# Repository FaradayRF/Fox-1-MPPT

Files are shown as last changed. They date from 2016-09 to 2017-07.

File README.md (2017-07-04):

# Fox-1-MPPT
This repository contains the Public Domain files of the [Radio Amateur Satellite Corporation](http://www.amsat.org) (AMSAT) Fox-1 satellite Maximum Power Point Tracker. This is a PCBA flying on the Fox-1 series of 1U cubesats which optimizes the power extracted from the six solar panels on the spacecraft using analog computing.

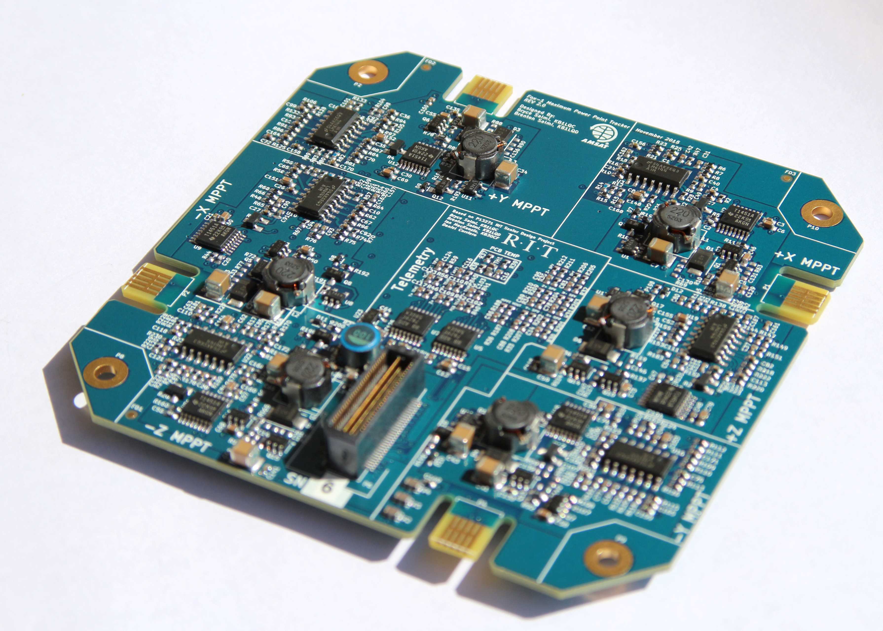
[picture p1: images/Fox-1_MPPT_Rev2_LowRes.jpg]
AMSAT Fox-1 MPPT


# Overview

The Fox-1 Maximum Power Point Tracker utilizes analog computing to track the solar panel voltage which generates the maximum amount of power from solar cells. It implements what is essentially a "temperature-based set-point constant voltage algorithm" MPPT. Since the solar cells are well-known, this design uses op-amps to compute the predicted voltage which will produce maximum power as fast as the analog bandwidth of the components used will allow it. Analog MPPT was chosen for it's "stateless" design due to radiation tolerance concerns of microcontrollers.

Revision 1.2 boards are Revision 1 PCB's with BOM modifications necessary for correct operation. This included stacking some capacitors ontop of feedback resistors in the RTD circuit for stability. Revision 1 PCB's are green soldermask in color. Revision 2 PCB's were created to adress these issues better and properly mount all parts with correct footprints and adress some other manufacturing needs. These boards are use a blue soldermask and the design files for the Rev 2.1 boards have been uploaded to this Github repository.

[READ THE FOX-1 MPPT TECHNICAL OVERVIEW TO UNDERSTAND THE PROJECT!](https://github.com/FaradayRF/Fox-1-MPPT/blob/master/Documents/Fox-1_MaximumPowerPointTracker.pdf)

# History
This project began as a [Rochester Institue of Technology](http://downloads.kicad-pcb.org/archive/KiCad_stable-2013.07.07-BZR4022_Win_full_version.exe) Multi-disciplinary Senior Design (MSD) project during the 2012-2013 school year. Originally the [P13271 AMSAT-MPPT](http://edge.rit.edu/edge/P13271/public/Home) project which successfully delivered a proof-of-concept MPPT intended for a 3U cubesat, the design was continued and modified for use on the smaller Fox-1 satellites which are 1U in size.

## Original Team
The original RIT team to create this MPPT included
* Bryce Salmi, KB1LQC
* Brenton Salmi, KB1LQD
* Ian MacKenzi, KB3OCF
* Daniel Corriero

Work was performed over two years between 2013 and 2015 by Bryce Salmi and Brenton Salmi to bring the design to flight status from the P13271 project as seen here.

# Flights
The Revision 1.2 and Revision 2.1 Maximum Power Point Trackers are currently slated to fly on several launches to Low Earth Orbit with more launches being sought after. These flights are accurate as of 9/3/2016.

### Fox-1Cliff and Fox-1D
Two MPPTs will fly aboard two cubesats on the same launch. These satellites are Fox-1Cliff and Fox-1D which are being sent up on the Spaceflight SHERPA payload on a [SpaceX Falcon 9](http://www.spacex.com/falcon9).

### Fox-1B "RadFxSat"
One MPPT will be flying on the Fox-1B cubesat set to launch aboard a ULA [Delta II](http://www.ulalaunch.com/Products_DeltaII.aspx) rocket.

### Fox-1E "RadFxSat-2"
One MPPT will be flying on the Fox-1E cubesat set to launch aboard a [Virgin Galactic Launcher One](http://www.virgingalactic.com/satellite-launch/) in December, 2017.

# Project Structure
## Hardware Files
All hardware files are located in the [Hardware/Rev2_1](https://github.com/FaradayRF/Fox-1-MPPT/tree/master/Hardware/Rev2_1) directory. They consist of [Kicad EDA](http://kicad-pcb.org/) files which were developed using [Kicad Build: 2013-07-07 BZR 4022](http://downloads.kicad-pcb.org/archive/KiCad_stable-2013.07.07-BZR4022_Win_full_version.exe) which is the July 2013 stable version of the EDA tool (Windows). Also placed into the hardware directory are the [project output files](https://github.com/FaradayRF/Fox-1-MPPT/tree/master/Hardware/Rev2_1/OutputFiles). These are the files which were used to order the PCBs and present an easy to use view of the design (PDF, Excel, Gerber, etc).

**Notable Documents**
* [MPPT Schematic PDF Export](https://github.com/FaradayRF/Fox-1-MPPT/blob/master/Hardware/Rev2_1/OutputFiles/TL1451_MPPT_Flight_Rev2_BW.pdf)
* [MPPT BOM](https://github.com/FaradayRF/Fox-1-MPPT/blob/master/Hardware/Rev2_1/OutputFiles/TL1451_MPPT_Flight_Rev2_BOM.xlsx)
* [MPPT Extra Components BOM](https://github.com/FaradayRF/Fox-1-MPPT/blob/master/Hardware/Rev2_1/OutputFiles/TL1451_MPPT_Flight_Rev2_Additional_BOM.xlsx)
 * Addition parts for the solar panels necessary for the MPPT to work
* [MPPT KiCad project file](https://github.com/FaradayRF/Fox-1-MPPT/blob/master/Hardware/Rev2_1/TL1451_MPPT_Flight_Rev1.pro)
* [KB1LQC KiCad schematic symbol library](https://github.com/FaradayRF/Fox-1-MPPT/blob/master/Hardware/Rev2_1/KB1LQC.lib)
* [KB1LQC KiCad PCBNew footprint library](https://github.com/FaradayRF/Fox-1-MPPT/blob/master/Hardware/Rev2_1/KB1LQC.mod)
* [MPPT PCB Fabrication Files](https://github.com/FaradayRF/Fox-1-MPPT/blob/master/Hardware/Rev2_1/OutputFiles/TL1451_MPPT_Flight_Rev2_1_FAB_Files.zip)
* [MPPT PCBA Assembly Files](https://github.com/FaradayRF/Fox-1-MPPT/blob/master/Hardware/Rev2_1/OutputFiles/TL1451_MPPT_Flight_Rev2_1_ASSEMBLY_Files.zip)

## Documents
The [documents folder](https://github.com/FaradayRF/Fox-1-MPPT/tree/master/Documents) contains support documents necessary to describe the design intentions and analysis of the MPPT.

**Notable Documents**
* [Fox-1 MPPT Technical Overview](https://github.com/FaradayRF/Fox-1-MPPT/blob/master/Documents/Fox-1_MaximumPowerPointTracker.pdf)
* [Fox-1 Satellite Solar Panel Calculations](https://github.com/FaradayRF/Fox-1-MPPT/blob/master/Documents/MPPT_Expected_Voltages_Fox-1.xlsx)
* [Fox-1 Solar Panel Telemetry Scaling](https://github.com/FaradayRF/Fox-1-MPPT/blob/master/Documents/PanelTemperatureScaling.xlsx)
 * Scaling telemetry downlinked from satellite over RF into Celcius from RTD circuit

## Images
The [images directory](https://github.com/FaradayRF/Fox-1-MPPT/tree/master/images) contains a select set of high-quality stock images showing the Rev 2 MPPT very clearly. Not much more needed to say about this :rocket:

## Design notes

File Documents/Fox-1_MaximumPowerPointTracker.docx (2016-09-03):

Date: September 3rd, 2016

Version: 1.2

Author: Bryce Salmi, KB1LQC

AMSAT Fox-1 Maximum Power Point Tracker

## Introduction

The Radio Amateur Satellite Corporation, AMSAT, has designed and built a series of 1U Cubesats referred to as Fox-1. Starting with these 1U Cubesats, AMSAT will build up intellectual property to leverage onto future satellite designs. A requirement for the Fox-1 satellites is an efficient way to maximize power generation from solar cells with a scalable Maximum Power Point Tracker, MPPT. Based on the Fox-2 design originally conceived by the P13271 senior design team (http://edge.rit.edu/edge/P13271/public/Home)[^1] at the Rochester Institute of Technology AMSAT has developed a radiation tolerant analog MPPT for use on the Fox-1 satellites. Lessons learned building the Fox-1 MPPT detailed in this document can also be rolled into any future Fox-2 MPPT design.

### Document History

DATE | VERSION | SUMMARY
January 21, 2015 | 1.0 | Initial creation of document
October 2, 2015 | 1.1 | Initial flight design
September 3, 2016 | 1.2 | MPPT Rev 1.2 and 2 Updates

### Document Scope

The purpose of this document is to clearly explain how the Fox-1 MPPT has been designed, how it operates, and to how any known failure modes or risks affect the spacecraft. PCB revision 1.1 is shown in this document but the design of Rev 1.2 and Rev 2 are discussed. It also assumes a basic level of electrical knowledge and leaves some calculations up to the reader with reference material noted.

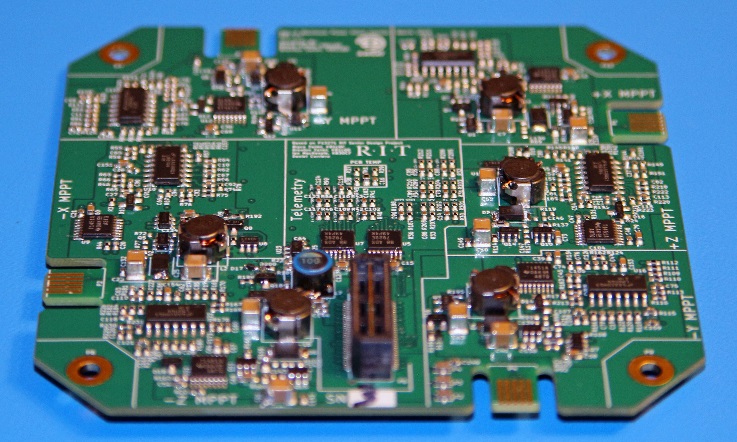
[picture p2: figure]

Figure 1: Fox-1 MPPT Rev 1.1

# Overview

The Fox-1 MPPT PCB contains six set-point constant voltage MPPT circuits[^2] with a single MPPT dedicated to each side of the spacecraft. Every side of Fox-1 contains two Spectrolab UTJ solar cells connected in series. All six MPPTs are combined through ideal diodes which allows for power sharing as the satellite rotates in orbit. The common diode OR’d output node then delivers the combined power of all sufficiently illuminated solar panels to the spacecraft main voltage bus. The Fox-1 MPPT also contains a telemetry circuit able to communicate with the Internal Housekeeping Unit, IHU, via I²C communications. It’s important to note that each of the six MPPTs is a zero fault tolerant design.

## Specifications

Parameter | Value | Units
Maximum Input Voltage | 50 | Volts
Minimum Input Voltage | 3.6 | Volts
Maximum Input Current (Per MPPT) | 0.443 | Amperes
Maximum Input Power (Per MPPT) | 2.57 | Watts
Maximum Output Current (Per MPPT) | 0.780 | Amps @ 3.3V Vout
Maximum Output Voltage | 4.33V | Volts
Maximum Switching Efficiency | ~88 | %
Maximum Tracking Error | +-5 | %
Temperature Range of Components | -40° to +125° | Celsius
Solar Cell Operating Temperature Range | -60° to +60° | Celsius

Table 1: Overall Fox-1 MPPT Specifications

Careful use of radiation tested components, shielding, and a stateless design in the critical MPPT feedback loops on Fox-1 has been implemented in order to promote a 5 year mission timeline and an estimated 30 kRad TID exposure. The stateless design hardens the MPPT to Single Event Upsets, SEU, and Single Event Latch-ups, SEL, which are expected during the mission. Table 1 documents the general specifications achieved as supported by engineering bring-up data.

## Spectrolab UTJ Solar Cells

Fox-1 was designed for use with two SpectroLab UTJ solar cells (http://www.spectrolab.com/DataSheets/TNJCell/utj3.pdf) in series on each solar panel with each cell having 27 cm² of area as shown in Figure 2. Table 11 in the Appendix shows the calculations of the maximum power point thermal drift. This information was used to design the MPPT as well as predict the amount of power available to Fox-1 at any panel temperature expected in orbit. The RTD measuring panel temperature is mounted to the back side of the solar panels out of direct sunlight.

Figure 2: Solar panels on Fox-1, a stowed antenna is shown on the closest facing solar panel

## MPPT PCB Configuration

### PCB Block Diagram

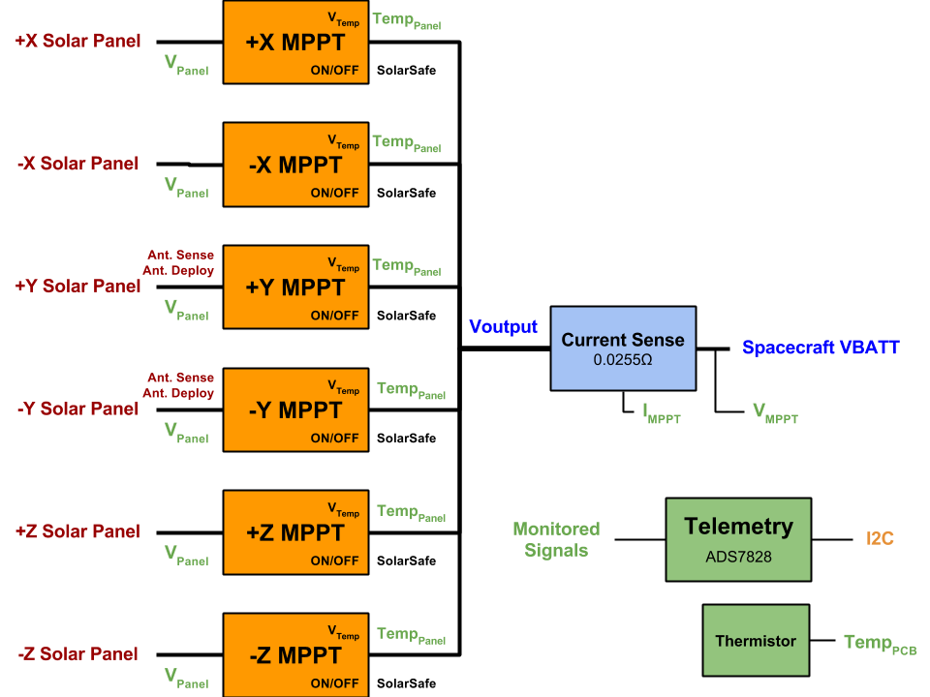
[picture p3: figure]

Figure 3: Fox-1 MPPT PCB block diagram containing six individual MPPT circuits combined together

Six Individual Maximum Power Point Trackers obtain power from their respective solar panels and if sufficient power is available then combine the generated power onto a common output
node through ideal diodes. The combined power is then fed through a current sense circuit before being sent to the Fox-1 “VBATT” node to power the satellite and charge the batteries. A telemetry system comprised of voltage dividers, RC low pass filters, and ADC’s gather engineering data for transmission to the IHU via I²C communications.

The design of the Fox-1 MPPT does not require a battery on the output of the PCB for proper operation. In the event of a battery failure where a properly designed circuit will disconnect the battery from the satellite power bus, the MPPT is fully capable of operation. The requirement for this operation however is that no more than maximum power available from the MPPT can be requested from the payload. This means that if the satellite can operate by never drawing more power than the lowest power available from solar panels then indefinite operation without a battery is possible.

Power is obtained from the X and Y axis panels through PCB edge connectors (Samtec MEC1-105-02-L-D-NP-A) and through the board-to-board connectors (Samtec QSH-030-01-L-D-A and QTH-030-02-L-D-A). Besides solar power, signals passing through these PCB edge connectors are the RTD connections (ground referenced) for measurement of each solar panel temperature as well as two antenna deploy and sense channels on the Y panels. The antenna deploy and sense connections are not thoroughly covered in this document, please refer to the schematic. All copper planes have been pulled back from the connector and a maximum of 20 mil traces were used to the connectors themselves to prevent heat loss to space from the MPPT PCB which is necessary for proper operation

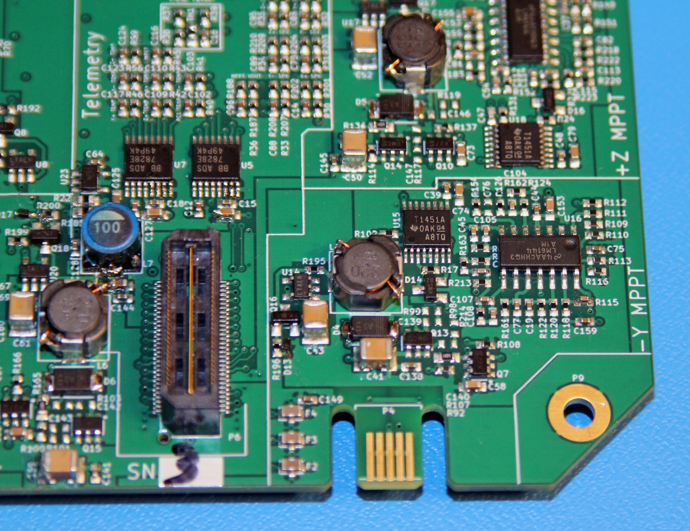
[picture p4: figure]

Figure 4: Samtec QTH-030-02-L-D-A board to board connector shown on left side of image, Samtec MEC1-105-02-L-D-NP-A edge connector shown near middle of image with male portion of connector made of PCB material

## PCB Design

Each PCB is a four layer board developed in the open source KiCad EDA (http://www.kicad-pcb.org/display/KICAD/KiCad+EDA+Software+Suite) (Build: 2013-07-07 BZR 4022)-stable on Windows. Gerber files were exported and sent to Advanced Circuits for fabrication. Since Gerbers are very portable file formats, AMSAT has the ability to use almost any manufacturer they choose. All relevant PCB processes have been documented in the “Drawings” Layer of the Gerbers.

### PCB Stackup

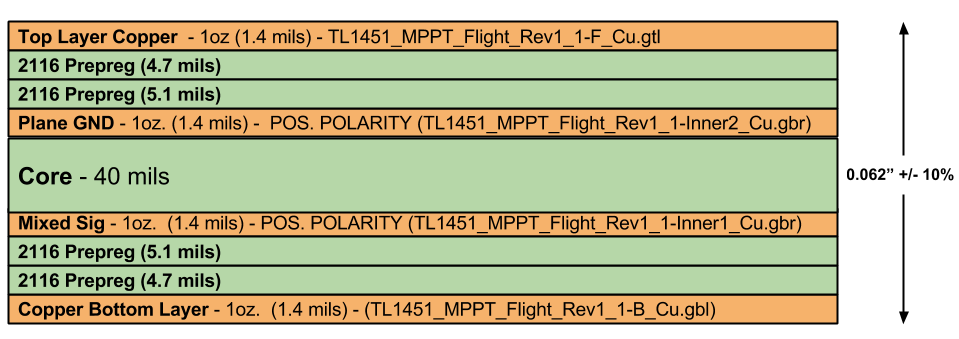
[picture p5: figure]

Figure 5: Four layer PCB stackup used on the Fox-1 MPPT Rev 1.1 PCB

Figure 6: Fox-1 MPPT Rev 1.1 PCB with top layer visible, all components other than stacking connector located on top layer

# Maximum Power Point Tracker Design

## MPPT Overview

The Fox-1 MPPT is designed as a temperature based set-point constant voltage MPPT and is implemented with analog circuitry to mitigate radiation events associated with holding state. There are two discrete feedback loops implemented in the design, the MPPT feedback loop and an output voltage regulation feedback loop. Both MPPT feedback loop and MPPT as a PCB will be referred to in this document and the context will determine the subject. The output voltage regulation circuitry limits the MPPT channel output voltage to 4.33V prior to the ideal diodes in order to protect the Fox-1 payload and batteries from overvoltage conditions. Using temperature based MPPT allowed power to be maximized without computational resources such as a microcontroller which requires state.

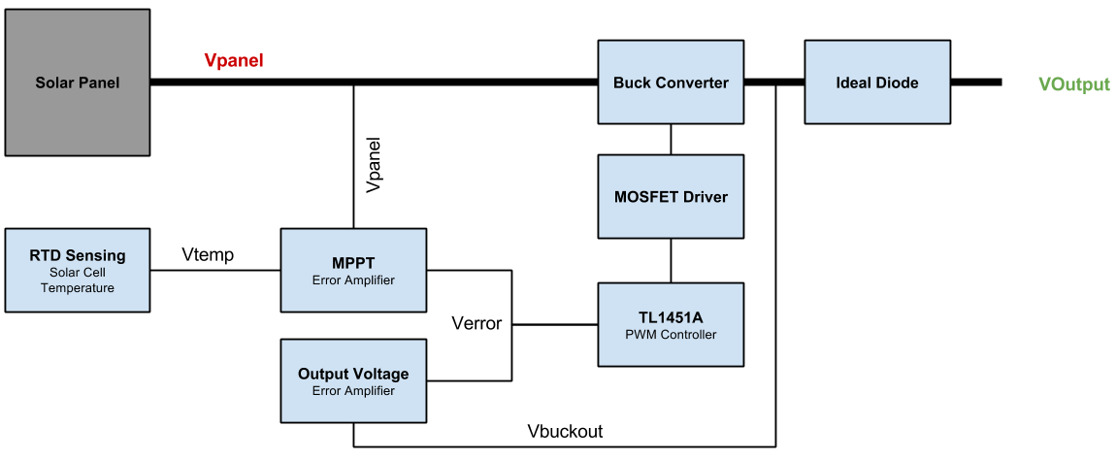
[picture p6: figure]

Figure 7: Fox-1 MPPT & voltage regulation feedback block diagram

As shown in Figure 7, there are two feedback loops used to control the TL1451A PWM controller. The internal TL1451A error amplifier is used as a unity gain buffer to directly pass the combined V_(error) signal from the external error amplifiers into the internal comparator used to generate the PWM signal. The inversions from the TL1451A open collector PWM output and PMOS gate create the following V_(error) to duty cycle relationship shown in Table 2.

V_(error) Change | PWM Duty Cycle
Increasing | Decreasing
Decreasing | Increasing

Table 2: Error voltage effect on the PWM duty cycle

Therefore, a simple resistive adder is used to combine both the MPPT error amplifier and output voltage regulation error amplifier signals. This results in the highest voltage error signal applied to the TL1451A winning control of the buck converter and forcing the lowest duty cycle of the two feedback loops to be implemented. This is extremely advantageous as shown later in this document.

## MPPT Schematics

The latest version of the schematics for the Fox-1 MPPT are located in the AMSAT SVN MPPT folder (http://amsatfox.org/repos/Fox1/PSU/MPPT/tags/Rev1_1/). Using KiCad to open “TL1451_MPPT_Flight_Rev1.pro” one has access to the schematics and PCB files within the KiCad EDA. An important note is that the libraries and footprints used for KiCad live in the SVN Power KiCad folder (http://amsatfox.org/repos/Power/kicad/) so those must be checked out too and Kicad may need to be told where they are on your computer to display properly. An annotated PDF version of the schematics is provided with this document.

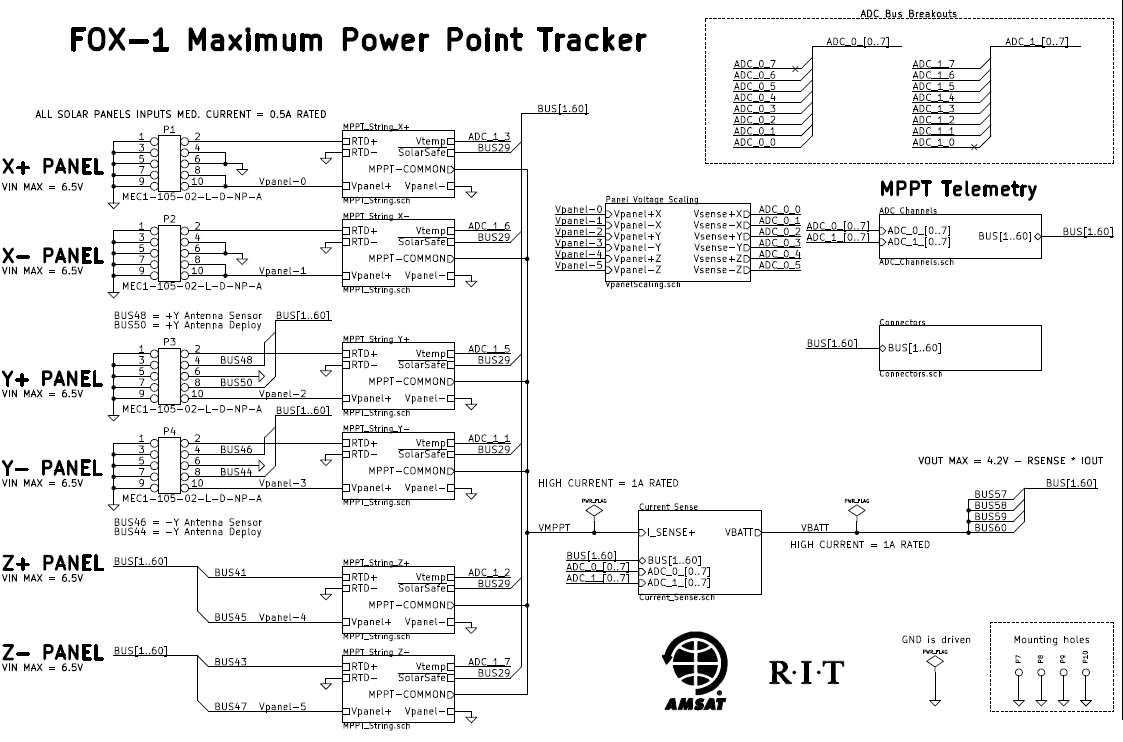
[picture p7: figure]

Figure 8: Main schematic page of the Fox-1 MPPT closely resembling the block diagram in Figure 3

The schematics are built up in a hierarchical arrangement as shown in Figure 8 much like block diagrams that contain sub-circuits within individual blocks. This makes understanding signal flows much easier and is very different from how EAGLE presents schematics. The main schematic page looks a lot like the overview block diagram shown in Figure 3. Hierarchical design results in a large number of schematics sheets due to channelization of the design. An annotated schematic included with this document at the 2015 AMSAT Symposium details all unique MPPT PCB circuits without duplication.

### Resistive Temperature Detector Circuitry

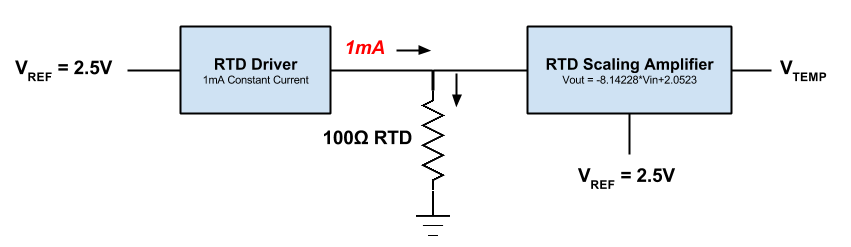
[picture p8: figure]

Figure 9: RTD drive and sensing block diagram

The AMSAT MPPT uses resistive temperature detectors, RTDs, to accurately measure solar panel temperature which is then used to predict the Maximum Power Point Voltage, MPPV. A constant current source forces exactly 1 mA into the RTD leaving only voltage to change with varying resistance as the RTD changes temperature. Both voltage and resistance are directly correlated as governed by Ohms law when using a constant current source. The measured voltage developed across the RTD is conditioned and amplified using a simultaneous equation based op-amp circuit implementing analog mathematics. This produces a voltage mimicking the solar panel voltage at MPPV and can be referenced by the MPPT error amplifier as it compares real panel voltage against this predicted reference voltage. This scaled voltage produced by the amplifier is referred to as V_(temp) . The RTD used for each panel is a PT100 type device, nominally 100Ω at 0°C (PTS080501B100RP100 (http://www.vishay.com/docs/28762/ptsserie.pdf)). RTDs are not thermistors, they use a pure metal such as nickel or platinum which have very accurate and predictable changes in resistance over temperature and nearly linear responses over the temperature ranges used.

Figure 10: Fox-1 MPPT RTD constant current driver

U3A of Figure 10 is a LM6144A op-amp configured as a constant 1 mA source. Its sole purpose is to force exactly 1 mA of current through the RTD. Note, C168 is used to slow down the op-amp to prevent oscillations. Figure 11 shows a LTSpice schematic of the 1 mA RTD driver (http://amsatfox.org/repos/Fox1/PSU/MPPT/Simulations/Flight_Current_Source.asc) and is used to describe the RTD circuit for the remainder of this description. The following equation determines the output voltage of the op-amp U1:

Vout=V_2 ((R_4)/(R_3 +R_4))×((R_2 +R_1)/(R_2))-V_1 ×(R_1)/(R_2)

Where V_2 is the reference voltage and V_1 is the grounded pad of R_1 . However, since R_1 ,R_2 ,R_3 , and R_4 are all 249KΩ we simplify the equation down to:

V_(OUT) =V_2 - V_1 =2.5 V

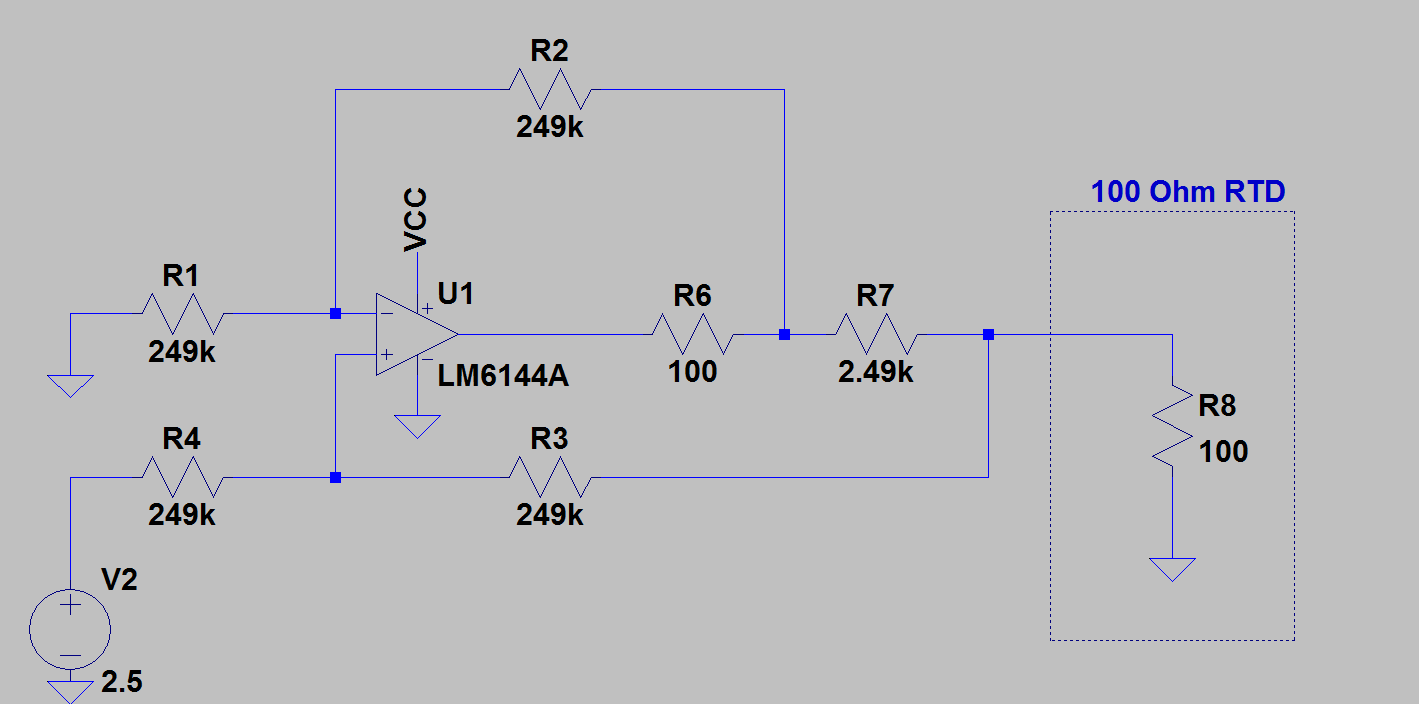
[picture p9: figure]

Figure 11: LTSpice 1mA RTD drive simulation schematic, capacitors not simulated.

Knowing we have 2.5V across R7 due to op-amp laws the following relationship for drive current is made.

R_7 =(V_2)/(I_(Drive))= (2.5V)/(1mA)=2.5KΩ

With 1 mA of drive current being forced into R8 (a 100Ω RTD) the voltage across it is predictable thanks to Ohms Law. 1 mA of drive current will dissipate about 100uW of power in the RTD and therefore cause minimal internal self-heating of the device and allows for accurate measurements. Table 3 shows several data points along the operating conditions expected in orbit for the solar panels and the respective RTD circuit voltage.

RTD Temperature | Voltage Across RTD
-60°C | 0.076V
0°C | 0.100V
28°C | 0.111V
+60°C | 0.124V

Table 3: Expected RTD voltages at 1mA drive current

The voltage across the RTD is very small (between 76mV and 124mV) and exhibits a positive thermal coefficient. This means the voltage increases as the temperature increases. However, the solar cells exhibit a negative temperature coefficient since the MPPT voltage decreases with a temperature increase. An op-amp configured to follow a polynomial equation is used to amplify the measured RTD voltage and flip the RTD voltage thermal coefficient. Essentially the op-amp performs the function y= -mX+b as covered in SLOA076 (http://www.ti.com/lit/ml/sloa076/sloa076.pdf) from Texas Instruments. The flight conditioning circuit implementing analog mathematics is shown in Figure 12. Note that the feedback capacitor C162 is used to slow down the op-amp and prevent oscillations.

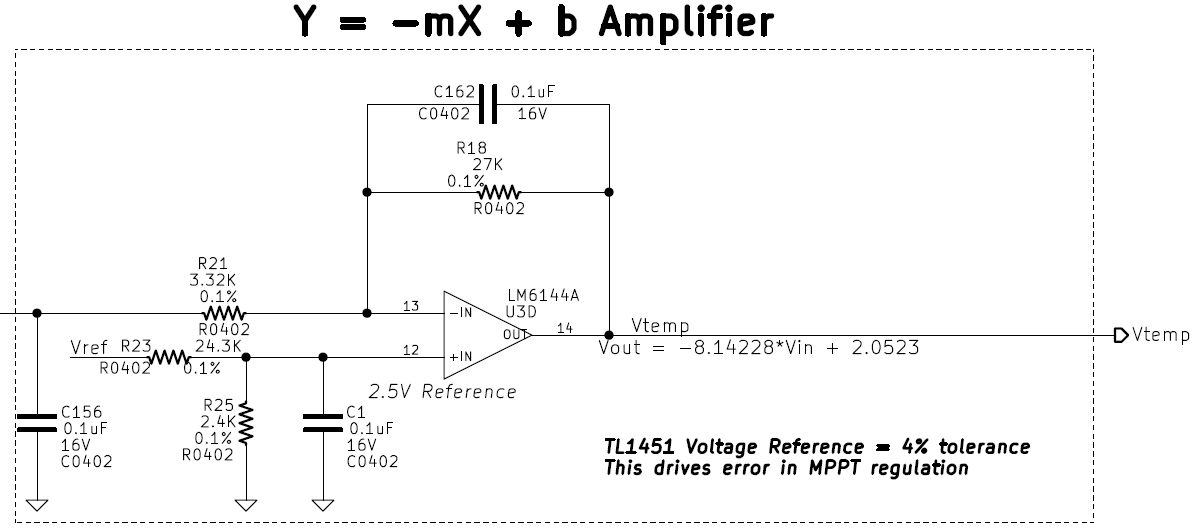
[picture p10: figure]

Figure 12: Scaling amplifier implemented on the Fox-1 MPPT panel temperature circuit which mimics solar panel MPPV

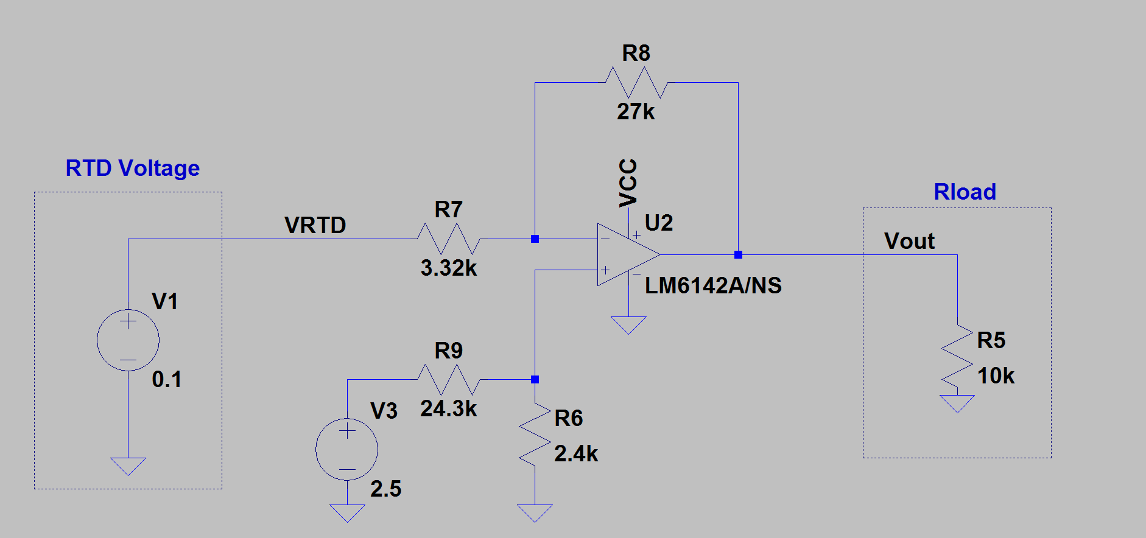
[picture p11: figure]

Figure 13: An LTSpice simulation of the RTD scaling amplifier, capacitors not simulated

Figure 13 shows the LTSpice simulation of the RTD conditioning amplifier referenced in the following description. Voltage source V1 represents the RTD voltage being measured and V3 represents the 2.5V reference from the TL1451A. A capacitor is added in the flight circuit across R6 to ground to low pass filter the voltage reference as shown in Figure 12. Another capacitor has been placed across R8 in the flight circuit to reduce the bandwidth of the circuit for stability also shown in Figure 12. A differential amplifier was not used to buffer the RTD since the solar panel PCBs have already been produced and were designed for thermistors which have one of the pins grounded and therefore the RTDs have a grounded pin too, rendering a differential amplifier not effective.

The TL1451A recommended error amplifier input voltage range is 1.05V to 1.45V so the panel voltage has been scaled by 0.245 using voltage dividers before being measured. The RTD predicted panel voltage must mimic this scaled voltage. The voltages in the Fox-1 Solar Panel Calculations in the Appendix show that minimum MPPV is obtained when high temperature panels are tracked at 4.28V and the maximum MPPV is 5.84V when the panels are tracked at low temperatures. This results in a MPPV voltage range of 1.048V to 1.430V present at the MPPT error amplifier during nominal power point tracking. These voltages are used as part of the simultaneous equations solved in SLOA076 (http://www.ti.com/lit/ml/sloa076/sloa076.pdf) and are given in Table 4 which are used to translate RTD measured voltages into the predicted MPPV reference voltage V_(temp) . The predicted voltage is also telemetered to sense panel temperature remotely from Earth via RF telemetry. With some basic mathematics described in the ADC section of this document the panel temperature can be resolved back from this voltage as measured by the ADC.

RTD Temperature | RTD Voltage | Vout Desired
60°C | 0.124V | 1.048V
-60°C | 0.076V | 1.430V

Table 4: Voltages used to solve for the scaling amplifiers component values

The values used for the output voltage of the scaling amplifier were chosen based on obtainable resistor values resulting in the following equation relating Vout of Figure 13 to RTD voltage:

V_(OUT) = -8.14228∙V_(IN) +2.0523

Figure 14 shows the RTD voltage versus scaling amplifier output voltage (predicted MPPV). The amplifier clearly amplifies the voltage as well as flips the temperature coefficient to match the Spectrolab solar cell based panel temperature coefficient.

Figure 14: Simulated RTD voltage input to the amplifier and output voltage representing the scaled panel voltage desired. The top graph shows the RTD voltage over the expected operating range while the bottom graph shows the resulting op-amp output voltage for the

### Totem Pole MOSFET Driver

The PWM output from the TL1451A is an open collector circuit and cannot provide a low impedance drive signal into the switching MOSFET gate. A low impedance drive signal is necessary to quickly turn the MOSFET on and off. A pull-up resistor, R11 in Figure 15, is connected to the open collector pin of the TL1451A where the PWM signal is output. More information can be found regarding MOSFET drivers in SLUP169 (http://www.ti.com/lit/ml/slup169/slup169.pdf) from TI.

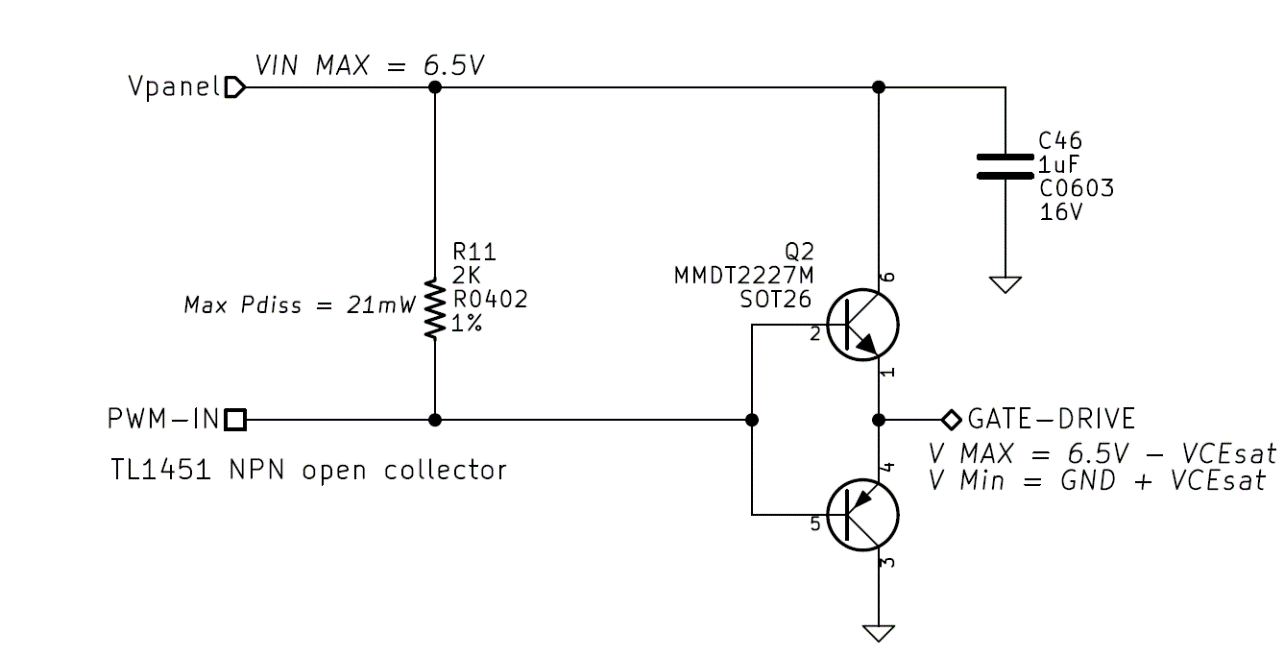
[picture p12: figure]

Figure 15: Open collector PWM output and totem pole MOSFET driver

The TL1451A output open collector stage inverts the signal produced by the PWM generator which is then fed into the totem pole driver (Q2 in Figure 15) which is a non-inverting circuit. The totem pole operates by pulling the MOSFET gate close to ground or close to the solar panel voltage, well into saturation or cutoff of the switching MOSFET. When the TL1451A open collector output pulls towards ground this will cause the PNP transistor base of Q2 (pin 5) to be a lower voltage than its emitter (pin 4 assumed at Vpanel) forcing the device into conduction and draining the MOSFET gate (GATE-DRIVE) into ground. Panel voltage from the open collector when it is open circuit will cause the PNP of Q2 to go into cutoff (base is higher voltage than emitter near ground) and then drive the NPN base (pin 2) to a higher voltage than the NPN emitter (pin 1) also near ground. This puts the NPN device into conduction and connects the solar panel voltage to the gate of the MOSFET. The voltage of the MOSFET gate will always be around a VBE below panel voltage or above ground during cutoff and saturation respectively.

### Buck Converter

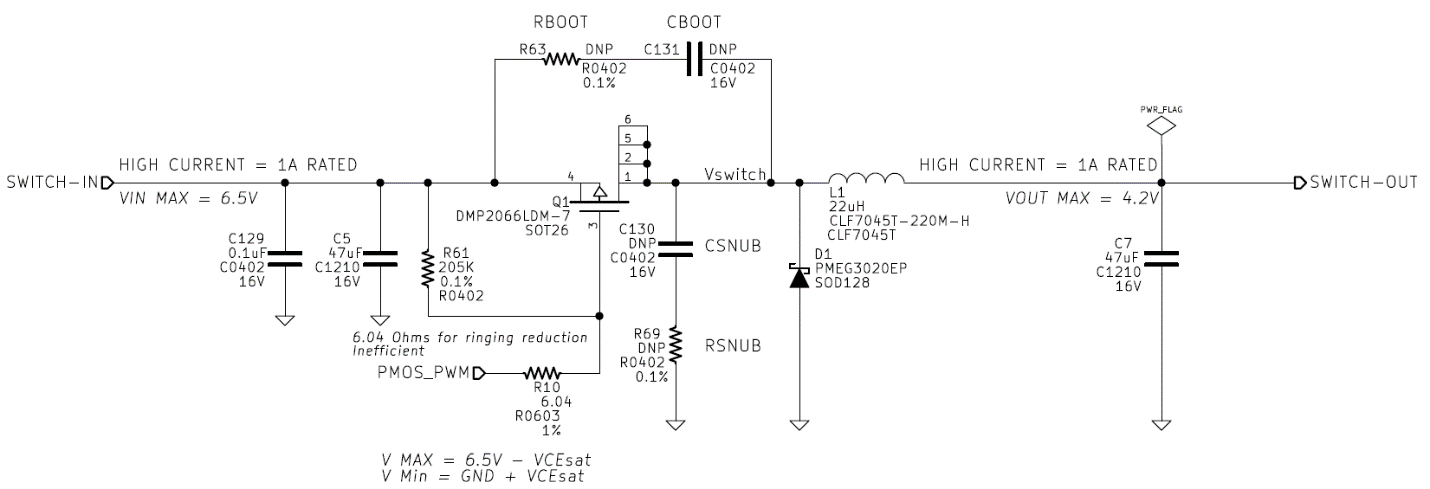
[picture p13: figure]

Figure 16: Fox-1 MPPT buck converter switching circuitry

A standard buck converter has been implemented on the Fox-1 MPPT as shown in Figure 16. The output of the totem pole MOSFET driver (GATE-DRIVE) is fed into PMOS_PWM which drives the gate of the P-channel device (PMOS) through a 6.04Ω resistor to dampen ringing. Standard buck converter design techniques were followed (SLVA477 (http://www.ti.com/lit/an/slva477b/slva477b.pdf)) to derive initial component values. The values in Table 5 show the parameters used to initially design the buck converter stage, these are assumptions about operating conditions prior to actually building the converter.

50mA was assumed to be the lowest current the buck converter would see when operating to guarantee continuous conduction mode and 780mA is the amount of current the coldest solar panel operating at MPPT would dump into a fully discharged battery at 3.3V. These are bounds which create a design capable of operating at all times in Fox-1. The design is non-synchronous and uses a catch diode as shown in Figure 16. Increased efficiency could be realized with a synchronous design in the future. Additionally, snubbing and boot RC circuits have been added to allow the control of ringing and edge rise time if necessary from the switching node to ground and the source to drain of the switching MOSFET. In the event that the series resistance to the gate is disconnected, a pullup resistor R61 has been implemented to provide fault tolerance by forcing the MOSFET off in that failure mode.

Parameter | Value | Unit
Minimum Input Voltage | 4.284 | Volts
Maximum Input Voltage | 6.464 | Volts
Minimum Output Voltage | 3.3 | Volts
Maximum Output Voltage | 4.33 | Volts
Minimum Current | 0.050 | A
Maximum Current | 0.780 | A
Assumed Efficiency | 90 | %
Minimum Duty Cycle | 0.5 | Ratio
Maximum Duty Cycle | 0.98 | Ratio

Table 5: Basic buck converter parameters used for the Fox-1 MPPT design

### MPPT Feedback

Maximum Power Point Tracking on Fox-1 is achieved by predicting the expected MPPV determined by the measured solar panel temperature using an RTD as previously described. The solar panel voltage, V_(panel) , and predicted MPPV, V_(temp) , are fed into a dedicated MPPT error amplifier built using an LM6144A op-amp as shown in Figure 17.

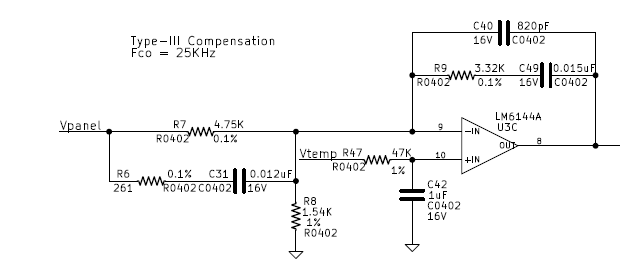
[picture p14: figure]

Figure 17: Maximum Power Point Tracking error amplifier

In Figure 17 the solar panel voltage is applied to the voltage divider created by R7 and R8 scaling the panel voltage by 0.245 and driving the inverting input of the op-amp U3C while the RTD measured V_(Temp) signal is applied to the non-inverting input as the reference voltage for the error amplifier. The op-amp output voltage, V_(error) , is determined by the following equation

V_(OUT) =A∙(V_(IN+) -V_(IN-) )=A∙(V_(Temp) -V_(panel) ∙0.245)

This means that given a large gain A from U3C, the output of of the error amplifier will decrease towards ground whenever the panel voltage is greater than the predicted V_(Temp) . Likewise, when V_(Panel) is lower than V_(Temp) the output voltage increases towards the VCC voltage rail (panel voltage). The following relationship can be determined:

V_(error) Change | PWM Duty Cycle Change | Panel Voltage | Output Voltage
Increasing | Decreasing | Increasing Voltage | Decreasing Voltage
Decreasing | Increasing | Decreasing Voltage | Increasing Voltage

Table 6: MPPT error amplifier output effect on solar panel and MPPT output voltage

Type-III compensation has been implemented due to the use of ceramic capacitors which exhibit a high frequency resonance with the buck converter and cause a near 180° phase-lag at the crossover frequency: a recipe for switch-mode converter instability. More information about compensating buck converters can be found in SLVA301 (http://www.ti.com/lit/an/slva301/slva301.pdf) from TI and specifically for Type-III in AN-1162 (http://www.irf.com/technical-info/appnotes/an-1162.pdf) from International Rectifier.

A crossover frequency of 25 KHz was chosen after building the MPPT and performing engineering tests. It was discovered that the TL1451A could not change the output voltage quick enough at its switching frequency when the bandwidth of the error amplifier was set much higher. Therefore, 25KHz was empirically chosen but cannot be drastically increased without instability. This bandwidth is faster than necessary to respond to a spinning Cubesat and provides adequate transient performance.

### Output Voltage Regulation Feedback

The purpose of the output voltage regulation error amplifier is to limit the maximum output voltage allowed to 4.33V at all times to protect the payload. A maximum of 4.33V accounts for some voltage drop from the ideal diode resulting in about 4.2V maximum at the battery. When this error amplifier is in control of the buck converter the maximum power of the solar panel is disregarded. This means the operating point is indeterminate but also unnecessary to know since full power is not needed. This occurs when the output voltage is close to 4.33V due to a fully charged battery and enough power from the panels is available to not discharge the batteries. Moving away from the maximum power point causes the extra power to dissipate as heat in the solar cells, radiating into space.

Much like the MPPT feedback error amplifier, the output voltage regulation error amplifier is implemented with a discrete LM6144A op-amp and compensated with a Type-III compensator. A 25KHz crossover frequency of the compensation network was also chosen to play nice with the TL1451A PWM controller. Refer to Figure 18 for the schematic of the voltage regulation error amplifier.

Figure 18: Output voltage regulation error amplifier

The output voltage regulation error amplifier is configured such that the 2.5V voltage reference (from the TL1451A) is applied to the inverting error amplifier input and the buck converter output voltage, V_(Output) (VMPPT), is applied to the non-inverting input. This is a classic voltage regulation error amplifier scheme.

The op-amp output voltage is determined by the following equation where A is the open loop gain and the output voltage is scaled to regulate to 4.33V. The resulting duty cycle characteristics can be observed in Table 7. Notice how the effects of the voltage regulation error amplifier signal are exactly the same as the MPPT error signal. The schematic in Figure 18 shows the Type-III compensation modified slightly to invert the output of the LM6144A used as a voltage regulator and match the necessary V_(error) polarity for implementation of the overall circuit characteristics detailed in Table 2.

V_(error) =A∙(V_(IN+) -V_(IN-) )=A∙(0.577∙ V_(Output) -V_(ref) )

Whenever the output voltage V_(Output) is larger than the 2.5V reference, the error amplifier increases its output voltage and PWM duty cycle will trend towards 0% in an effort to reduce V_(Output) . Consequently, whenever V_(Output) is lower than the 2.5V reference, the error amplifier signal will trend towards ground and the duty cycle will trend up towards 100% in an effort to increase the output voltage.

V_(error) Change | PWM Duty Cycle Change | Panel Voltage | Output Voltage
Increasing | Decreasing | Increasing Voltage | Decreasing Voltage
Decreasing | Increasing | Decreasing Voltage | Increasing Voltage

Table 7: Output voltage regulation duty cycle characteristics

### TL1451A Pulse-Width Modulation Controller

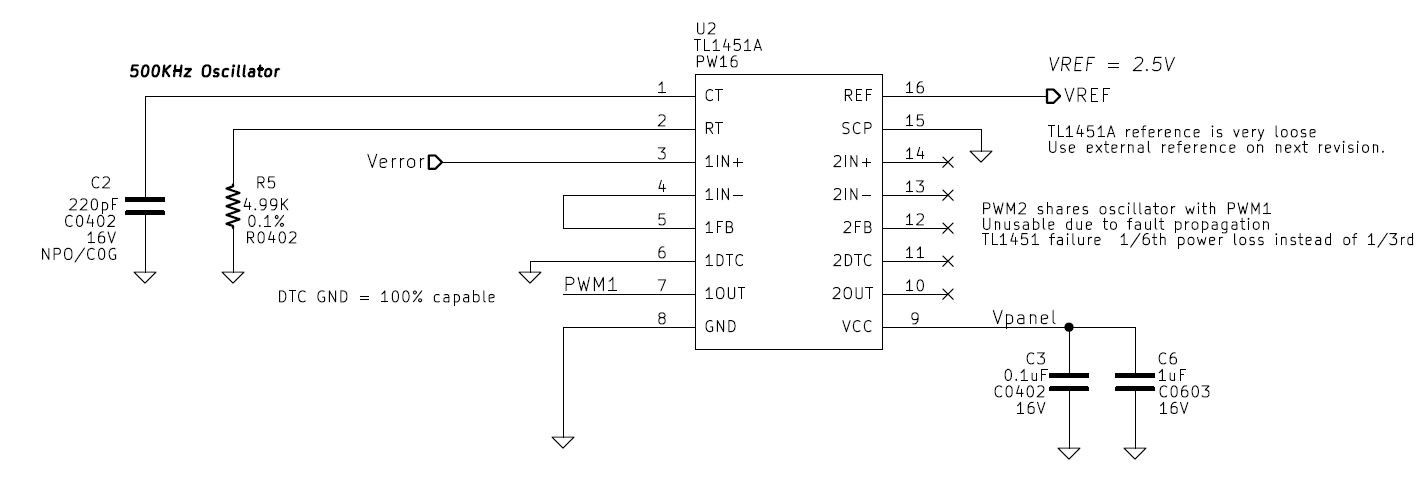
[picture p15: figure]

Converting error signals into Pulse-Width Modulation, PWM, signals is the job of the Texas Instruments TL1451A PWM controller (http://www.ti.com/lit/ds/symlink/tl1451.pdf) shown in Figure 19. This IC provides two synchronized PWM circuits but only one is used on Fox-1, coupling of failure modes of a single TL1451A removing two MPPTs from service was unwarranted. It was also the only PWM controller IC found to operate at the low voltages required and most ASIC MPPTs could not operate above panel voltage of 5V. The TL1451A obtains power directly from the panel it’s controlling and therefore it turns on when the panel reaches 3.6V, well above the LM6144A op-amp providing the input error signals which turns on at 1.8V. Thus ensuring valid input signals when powered on. The PWM generator uses an RC oscillator comprised of C2 and R5 running the circuit at a nominal 500 KHz. Frequency stability is not critical but thermal stability is highly recommended. The internal error amplifier is setup in a unity-gain configuration and simply buffers the externally generated error signals coming from the MPPT and voltage regulation error amplifiers detailed earlier.

Figure 19: The TL1451 circuitry on Fox-1 used to convert error signals into PWM signals controlling the buck converter

As shown in Figure 20, the TL1451A uses the error signal from Error Amplifier 1 to compare with a triangle wave generated by the oscillator. The dead time control, DTC, pin is grounded in Figure 19 as it is disabled. Short-circuit protection, SCP, is also grounded and therefore disabled since solar panels effectively limit the short circuit current. The error signal from Error Amplifier 1 (unity gain) is sent into the PWM comparator and then into an AND gate (always passes due to DTC pin configuration) which drives an open-collector NPN output transistor. Figure 21 shows the error signal and corresponding waveforms related to the TL1451A.

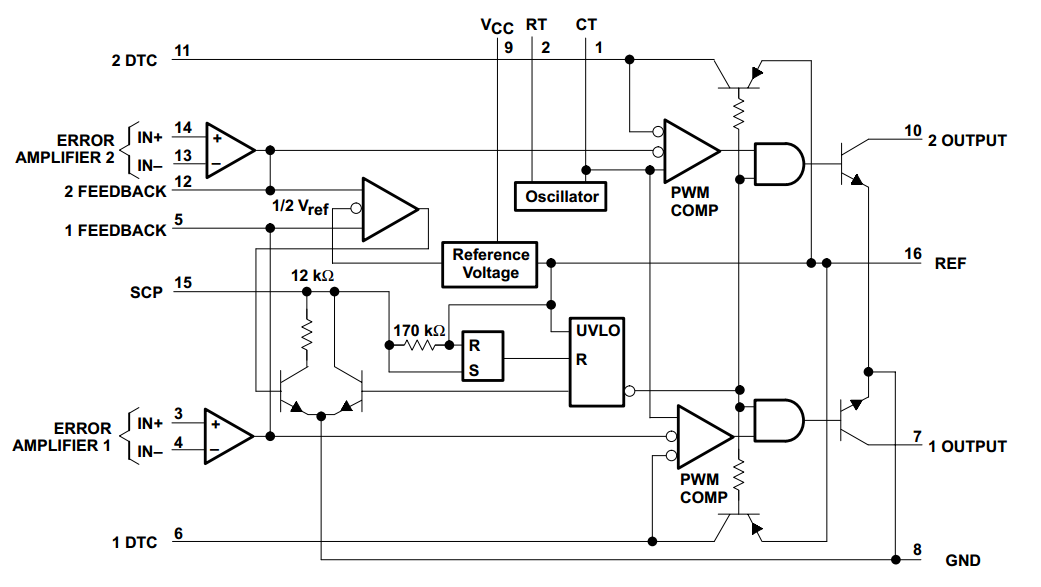
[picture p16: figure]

Figure 20: TL1451 block diagram from TI's datasheet SLVS024E

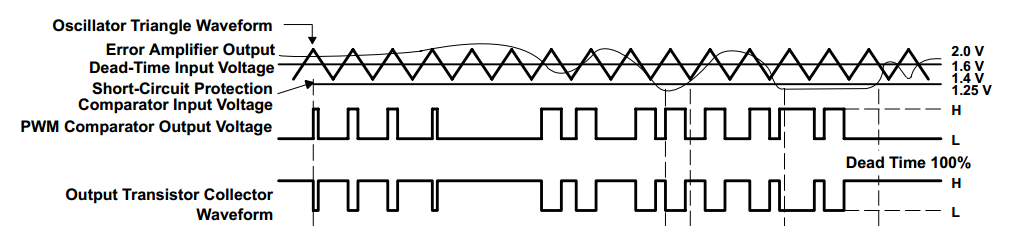
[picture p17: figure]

Figure 21: Example error amplifier to PWM open collector output signal path from TI’s datasheet SLVS024E

The magic inside the Fox-1 MPPT happens at the output of the MPPT and voltage feedback error amplifiers shown in Figure 22. Both error signals are combined with 2KΩ resistors acting as voltage adders. This combined error signal is sent directly into the TL1451A error amplifier. Diodes were originally used to combine signals but it was later realized that the TL1451A could sink enough current from the error amplifiers to cause damage as the TL1451A was designed to use a feedback signal from a voltage divider which is high impedance and not from low impedance op-amp outputs.

Figure 22: MPPT and output voltage regulation error amplifiers combined signals sent into TL1451A error amplifier

The resulting effect of the combined error signals in Figure 22 is that the highest voltage error amplifier always wins control of the TL1451A. As noted in Table 2, an increasing error signal demands a lower duty cycle which means this circuit properly interfaces with the PWM controller. Once an error amplifier voltage drops below the other, it will start to pull the combined signal down. However, the amplifier attempting to drive the highest output voltage will simply source more current into the combined node in efforts to maintain regulation. The voltage drop across R1 does not matter because the error amplifiers will automatically compensate for this loss as regulation is maintained provided enough voltage headroom.

#### How MPPT and Voltage Regulation Coexist

It’s important to remember the overall interaction of the MPPT and voltage regulation feedback loops must coexist with the input and output power scenarios presented to Fox-1. When the Fox-1 payload is not transmitting and has just finished charging its batteries in full sunlight the panels will be capable of delivering maximum power to the satellite which is no longer using all the power generated. At this point the MPPT feedback loop is in control. Since more power is delivered to the output than needed the output voltage rises and attempts to go above 4.33V. At this point the voltage regulation error amplifier output rises quickly and overtakes the MPPT voltage in an effort to reduce the duty cycle and maintain output regulation at 4.33V. This causes the solar panel voltage to rise towards open circuit voltage as less current is being pulled from it, delivering less power to the payload which reduced output voltage. Meanwhile, the MPPT feedback loop rails low in an effort to increase the duty cycle, trying to reduce the panel voltage towards MPPV but the output voltage regulation error signal will remain in control since highest error amplifier voltage wins control of the TL1451A. Saturation of the op-amps as they rail towards ground in any case is not really an issue since spacecraft rotation is on the order of a few rotations per minute which allows the op-amps ample time to desaturate.

When Fox-1 enters eclipse with fully charged batteries it will discharge them during the eclipse period. The MPPT is off during this time, however when Fox-1 just comes out of eclipse into sunlight the batteries will be discharged which forces the MPPT output voltage lower than 4.33V. The output voltage of the converter is governed by the battery voltage. The output voltage regulation error amplifier attempts to increase duty cycle to increase the output voltage and increases charging current into the batteries, pulling more current from the solar panels. This continues until the MPPT error amplifier senses that the solar panel voltage has decreased to the predicted MPPV. At this point the voltage regulation error signal has decreased in an effort to increase duty cycle as the panel voltage lowered; delivering more energy to the output in order to maintain 4.33V. However, the MPPT error signal has also started to increase and will eventually be higher than the voltage regulation error signal causing the maximum power point to be tracked when it surpasses the voltage regulation output voltage. This remains true until the converter output voltage rises towards 4.33V when the batteries have fully charged and the voltage regulation loop regains control.

The end result is a feedback loop configuration on Fox-1 that only delivers maximum power to the satellite when the satellite demands it; otherwise the MPPT circuitry uses its voltage regulator feedback loop to protect the downstream electronics and moves the solar panels away from MPPT. The MPPT is not expected to properly charge the batteries, which is the job of the battery PCB and circuitry.

### Ideal Diode

Each of the six MPPTs has an ideal diode immediately following the buck converter as shown in Figure 23. This provides an efficient power diode-OR function and permits power sharing between MPPTs. Each ideal diode connects to a common output node that is fed into a current sense amplifier before sending power to the Fox-1 payload. The LTC4411 (http://cds.linear.com/docs/en/datasheet/4411fa.pdf) (U1) provides the ideal diode function with only 140mΩ of resistance which equates to 85mW of loss at the maximum output current of 780 mA. The output status pin is not used and the control pin which is active low is pulled up to the solar panel voltage whenever the solar safe circuit is enabled (remove before flight pin inserted); disabling the MPPT from powering Fox-1 at all. This is a launch vehicle safety feature demanded by some launch providers.

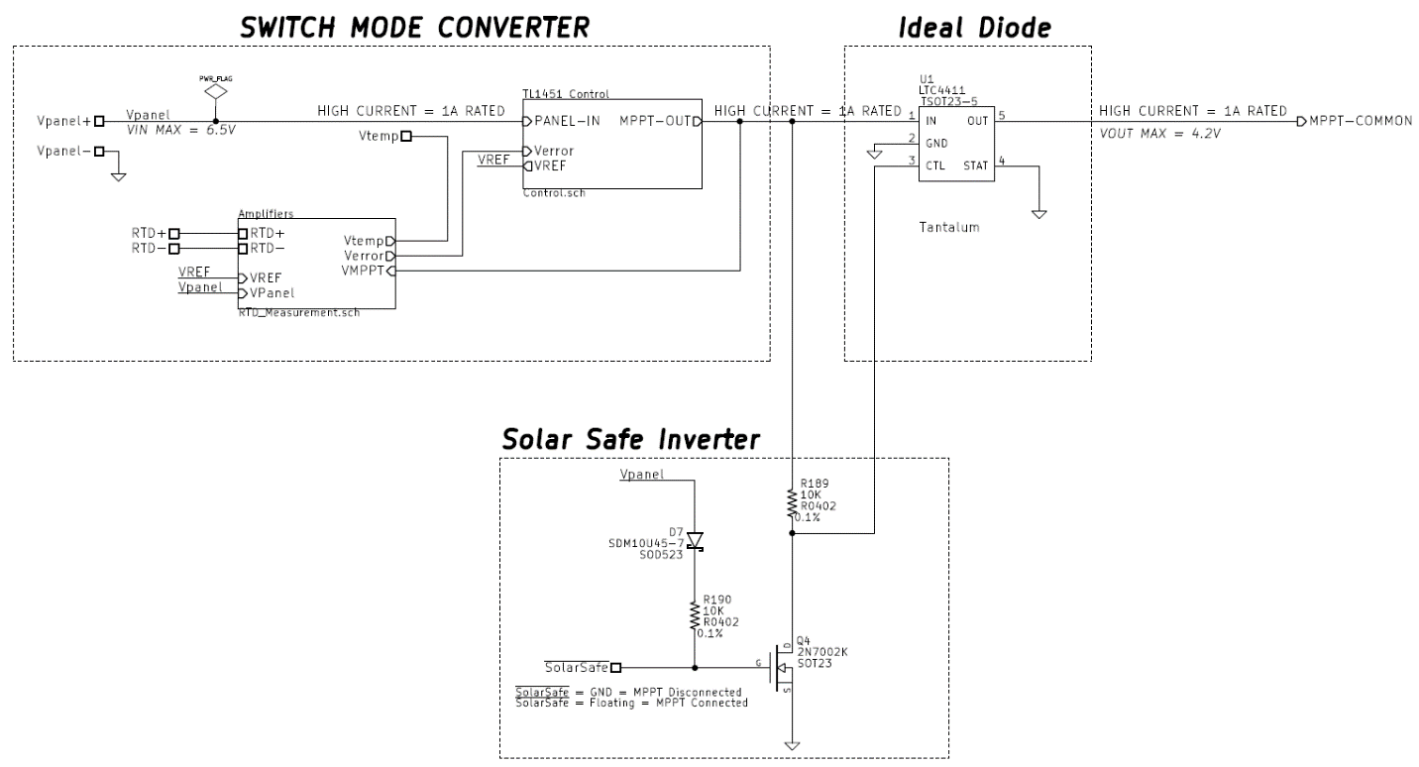
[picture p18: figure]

Figure 23: The LTC4411 ideal diode and accompanying solar safe circuitry shown with the MPPT converter circuitry

#### Solar Safe

In an effort to comply with PPOD and launch vehicle integration needs, the solar safe circuit is used to disconnect all MPPT circuits from the satellite, thus ensuring there is no way the satellite can obtain power while the remove before flight, RBF, pin is inserted. The solar safe signal is active low and is essentially a shorting bar to ground. Therefore while the RBF pin is inserted into its hole on Fox-1 the gate of Q4, is pulled to ground and turned off. This forces the ideal diode U1 in Figure 23 to turn off because the control pin is pulled high when the MPPT circuit turns on in sunlight.

Since the gate of Q4 is pulled up through R190 and D7, the shorting RBF pin will conduct through the respective devices to ground. R190 limits the current and D7 is used to prevent a reverse conduction path between each panel. When the RBF pin is the gate of Q4 is pulled up when the solar panel is in sunlight causing Q4 to conduct, pulling the LTC4411 control pin to ground and enabling the flow of current onto the satellite power bus from each MPPT.

Solar Safe is a common node among all six MPPT’s of Fox-1. A single piece of Foreign Object Debris, FOD, or other fault pulling this node to ground in flight will completely disable all MPPT’s. Disconnecting all MPPTs will cause the satellite to fail once the batteries have been depleted as they can no longer charge.

### Telemetry Circuitry

The telemetry circuitry on the Fox-1 MPPT consists of analog voltage, current, and temperature sensing which are digitized by two 12-bit ADS7828 (http://www.ti.com/lit/ds/symlink/ads7828.pdf) ADC’s. Power for all sensing circuitry is obtained from the IHU which is disabled when an IHU failure occurs. Sensor Power is provided from the PCB stack connector and is a regulated 3V. The idea for obtaining power from the IHU is that if/when the IHU gracefully fails it will go into a safe state which disconnects all telemetry power turning off the ADCs and support circuitry for them. This is largely a legacy requirement due to original Fox-1A circuitry designs.

#### PCB Temperature Thermistor Scaling

PCB temperature is measured by a thermistor powered by sensor power (3V) and attached to a linearizing circuit. The thermistor, TH1, is shown in Figure 24 and is linearize by R37, R38, and R39 while stabilized by C16. The resulting voltage is connected to Channel 0 of ADC 2. The linearizing circuit is based on the output from the Vishay Resistor/Thermistor Netsim Tool (http://www.vishay.com/resistors-non-linear/resistor-thermistor-netsim/).

Figure 24: NTC thermistor linearizing circuit used to measure PCB temperature

#### Output Current Sense

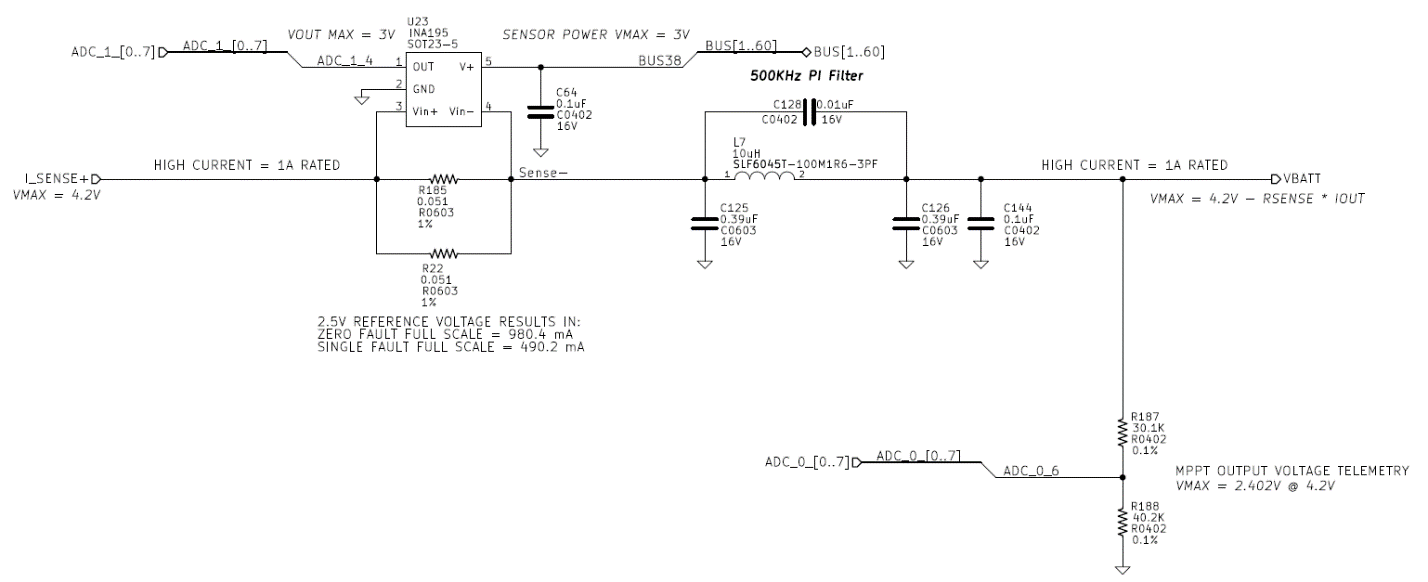
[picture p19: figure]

Figure 25: All MPPTs combine and feed through a current sense circuit for telemetry purposes

The common I_SENSE+ node is a combination of all six MPPT outputs following their respective ideal diodes. The INA195 (http://www.ti.com/general/docs/lit/getliterature.tsp?genericPartNumber=ina195&fileType=pdf) from Texas Instruments is a 100V/V current shunt monitor measuring the voltage across a parallel combination of R22 and R185 shown in Figure 25. The shunt resistors are dual redundant to protect against a bad solder or vibration damage on one resistor causing complete current path loss and consequently mission failure.

In a parallel configuration the current shunt is nominally 0.0255Ω and will drop 19.9mV at the maximum output current of 780mA which is amplified by the INA195 to 1.989V. This dissipates about 15.5mW of power between both resistors at maximum current. In a fault case of either shunt resistor, a single 0.051Ω resistor will dissipate 31mW and the INA195 will attempt to amplify the signal up to 3.9V at maximum current but the output will be saturated at 3V from sensor power provided by the IHU. Table 8 shows the nominal and fault operation characteristics of the amplifier. Since the maximum output current from a single MPPT is 780mA, a failure of R22 or R185 will be observable as 980 mA whenever the current is expected to go over 490mA due to ground telemetry scaling coefficients. This should be obvious when compared to nominal operation data as full scale operation should not be common.

Shunt Resistance | ADC Full Scale Current | Mode
0.0255Ω | 980mA | Nominal
0.051Ω | 490mA | Fault

Table 8: Current shunt and amplifier values in nominal and fault modes of R22 and R185

Following the current sense amplifier is a capacitive input PI filter used to provide a low pass filter for MPPT voltage powering Fox-1. The parallel capacitor across L7 provides a deep null at the switching frequency.

#### Voltage Scaling Circuitry

The voltage dividers shown in Figure 26 scale all panel voltages by 0.428. This scaled voltage is then input into the low pass filters of the ADCs detailed next.

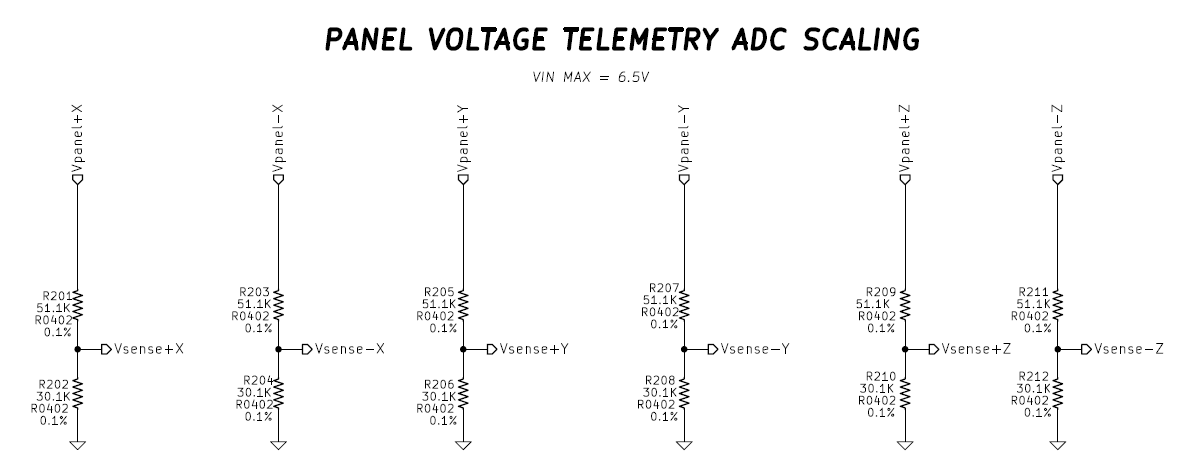
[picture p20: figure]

Figure 26: Voltage dividers used to scale solar panel voltages

#### Analog-to-Digital Converters

The ADS7828 (http://www.ti.com/lit/ds/symlink/ads7828.pdf) ADCs communicate to the IHU via the I²C protocol over the PCB stack connectors. These 12-bit ADCs are powered from 3V sensor power provided by the Fox-1 IHU card. The reasoning for this power configuration is to ensure that the ADC’s are only turned ON/OFF when the microcontroller is operating correctly. Internal 2.5V references are used by the ADS7828 ADCs as commanded by the Fox-1 IHU via I²C. This means each bit represents 610.4 uV on the ADC input, providing adequate resolution. Figure 27 and Figure 28 show the ADCs as implemented on the Fox-1 MPPT PCB.

16 Hz low pass filters are used to filter out high frequency content as telemetry is only sampled once every 15 seconds. This was deemed a suitable and realistic filter value. On-board IHU oversampling could be used to prevent aliasing but most signals of interest are so low frequency that avoiding aliasing is not a huge concern and that topic is outside the scope of this document. The filters also provide current limiting functionality for ADC protection. The series 10KΩ resistors limit current into the ADC to no more than about 320uA per channel when the ADC is on and about 650uA per channel when the ADC is off. It is important to remember that this only occurs during fault cases if signal conditioning circuits short panel voltage to the low pass filters. The limiting resistance works in conjunction with internal protection diodes inside the ADS7828 which conduct into the sensor power rail and ground.

Figure 27: ADC 1 used to obtain PCB temperature, solar panel temperature, and output current telemetry.

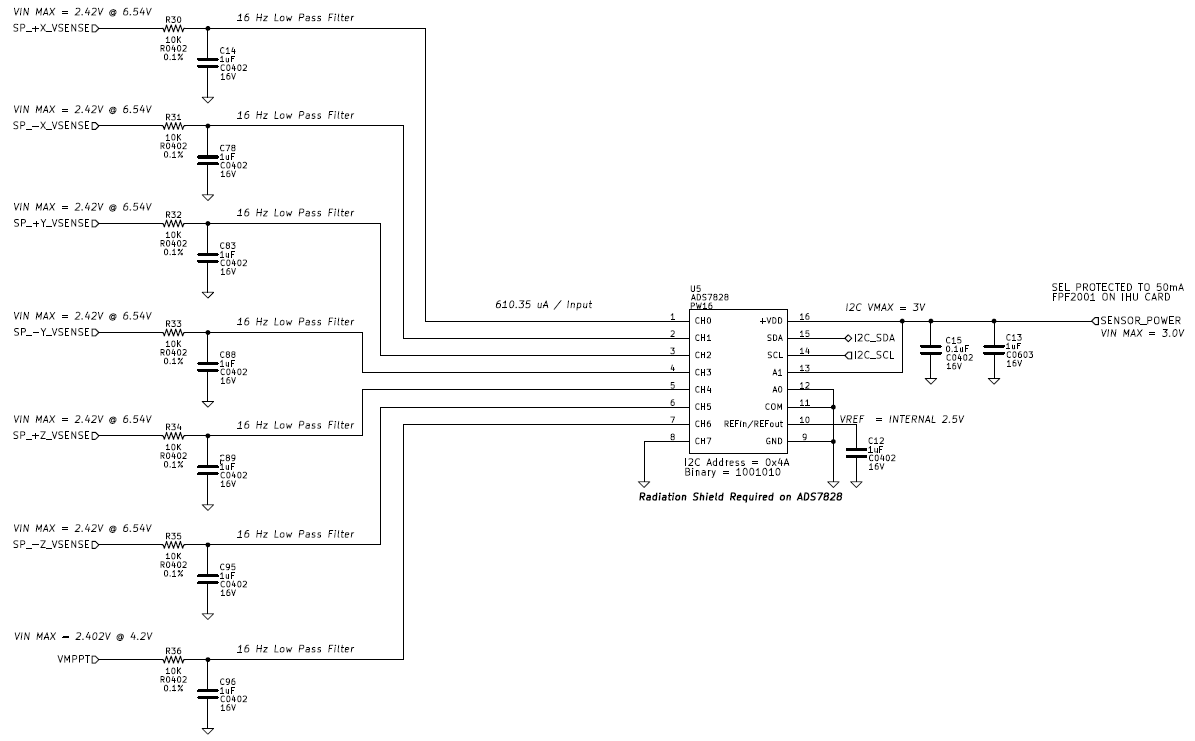
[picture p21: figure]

Figure 28: ADC 2 used to obtain solar panel and MPPT output voltage telemetry.

The I²C communications defined in the AMSAT PSU to IHU ICD (http://amsatfox.org/repos/Fox1/Systems/PDF/Fox1%20IHU%20PSU%20ICD.pdf) states that the IHU will be the I²C master while the MPPT PCB ADCs will be slaves and that communications are established at 10 KHz. For more I²C details please refer to the AMSAT PSU to IHU ICD.

ADC 1 (I²C Address = 0x49)
ADC Channel | Telemetry Signal | Bit Scaling (Y = mX + b)
0 | PCB Temperature | Same as LDO PCB on Fox-1A
1 | -Y Solar Panel RTD Resistance | m = -0.074961, b = 252.1
2 | +Z Solar Panel RTD Resistance | m = -0.074961, b = 252.1
3 | +X Solar Panel RTD Resistance | m = -0.074961, b = 252.1
4 | MPPT Output Current | m = 2.3935E-4, b = 0
5 | +Y Solar Panel RTD Resistance | m = -0.074961, b = 252.1
6 | -X Solar Panel RTD Resistance | m = -0.074961, b = 252.1
7 | -Z Solar Panel RTD Resistance | m = -0.074961, b = 252.1

Table 9: ADC 1 telemetry signals and scaling factors

ADC 2 (I²C Address = 0x4A)
ADC Channel | Telemetry Signal | Bit Scaling (Y = mX + b)
0 | +X Solar Panel Voltage | m = 0.001647, b = 0
1 | -X Solar Panel Voltage | m = 0.001647, b = 0
2 | +Y Solar Panel Voltage | m = 0.001647, b = 0
3 | -Y Solar Panel Voltage | m = 0.001647, b = 0
4 | +Z Solar Panel Voltage | m = 0.001647, b = 0
5 | -Z Solar Panel Voltage | m = 0.001647, b = 0
6 | MPPT Output Voltage | m = 0.001647, b = 0
7 | UNUSED (Grounded) | NONE

Table 10: ADC 2 telemetry signals and scaling factors

### RTD Panel Temperature Scaling

Solar panel temperature is measured by a RTD on each solar panel and analog mathematics performed by op-amps condition this voltage to mimic the solar panel MPPV. These mathematics can be reversed to directly calculate RTD resistance. Table 9 contains the RTD scaling values which compute the resistance in Ohms from the bit value of the ADC. The ADC scaling values implement a simplified form of the equation below

R_(RTD) (Ω)= [(ADC Bits ×((2.5V)/4096)-2.0523)/(-8.14228)]×(1/(0.001A))

All values used to determine the RTD scaling values were rounded to the 6th decimal place as this equation is pure mathematics and considered ideal. The TL1451A reference voltage has a pretty loose initial tolerance and essentially must be calibrated out to make the temperature sensing via ADCs very accurate. This is an MPPT specific process that results in six calibration values for each satellite and is outside the scope of this document. A cubic fit (http://www.mosaic-industries.com/embedded-systems/microcontroller-projects/temperature-measurement/platinum-rtd-sensors/resistance-calibration-table) is used to convert RTD resistance into degrees Celsius. The basic formula for a cubic fit of a PT100 RTD is:

Temperature (C)= -247.29+2.3992×R+0.00063962×R^2 +1.0241E-6 ×R^3

# Test Results

Testing was performed using a combination of digital multimeters, an active load, an ArduinoTM with a current sense circuit and I²C communications, and a digital oscilloscope. Various other tools were used but are not relevant to this document. Circuit operation as well as performance data will be showcased in an annotated form.

## MPPT Operation

Operation of the MPPT is clearly shown in Figure 29. A 2.5 Farad super capacitor was used as a battery simulator to hold up the output voltage and allow plotting of a nice graph. As shown, the capacitor started fully charged at about 4.25V and was constant current discharged down to 3.3V where the load was removed. More power was demanded from the MPPT PCB than the maximum power the solar panel simulators could provide causing a slow but linear decrease in panel voltage. The super capacitor was then allowed to charge back up. It’s obvious to see that the panel voltage was near the open circuit voltage when the capacitor was fully charged but as the capacitor voltage decreased the MPPT feedback loop kicked in and forced the panel down to about 4.8V to operate at maximum power (+-5% error at 0C). When the capacitor charged back up the MPPT feedback loop lost control and the voltage regulation feedback loop took over limiting capacitor voltage but allowing panel voltage to rise.

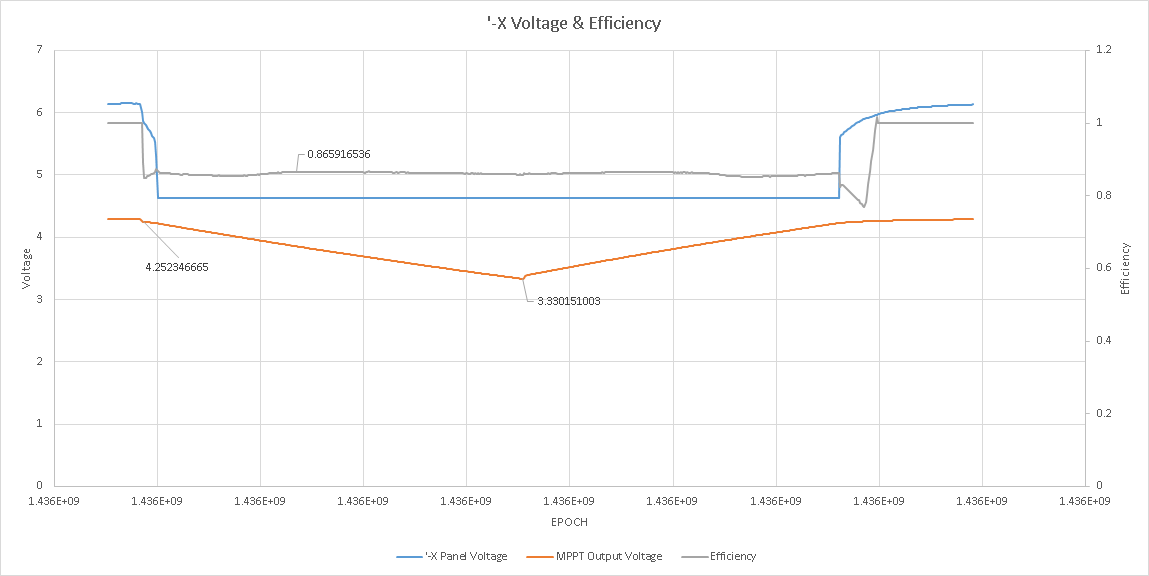
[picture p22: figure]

Figure 29: -X Panel operation as obtained by ADC telemetry through an ArduinoTM test setup and an external current sense to computer input and output power for efficiency calculations

Figure 30 nicely plots the input and output power of the MPPT and the resulting efficiency. Numbers are only valid during the time the test is occurring. The output power has a linear decreasing slope which is caused by series resistance from the buck converter, ideal diode, and current sense circuits. Ohm’s law! The power reaching the MPPT output drops as I²R losses increase when output current increases as the capacitor voltage decreased and conservation of power must be maintained.

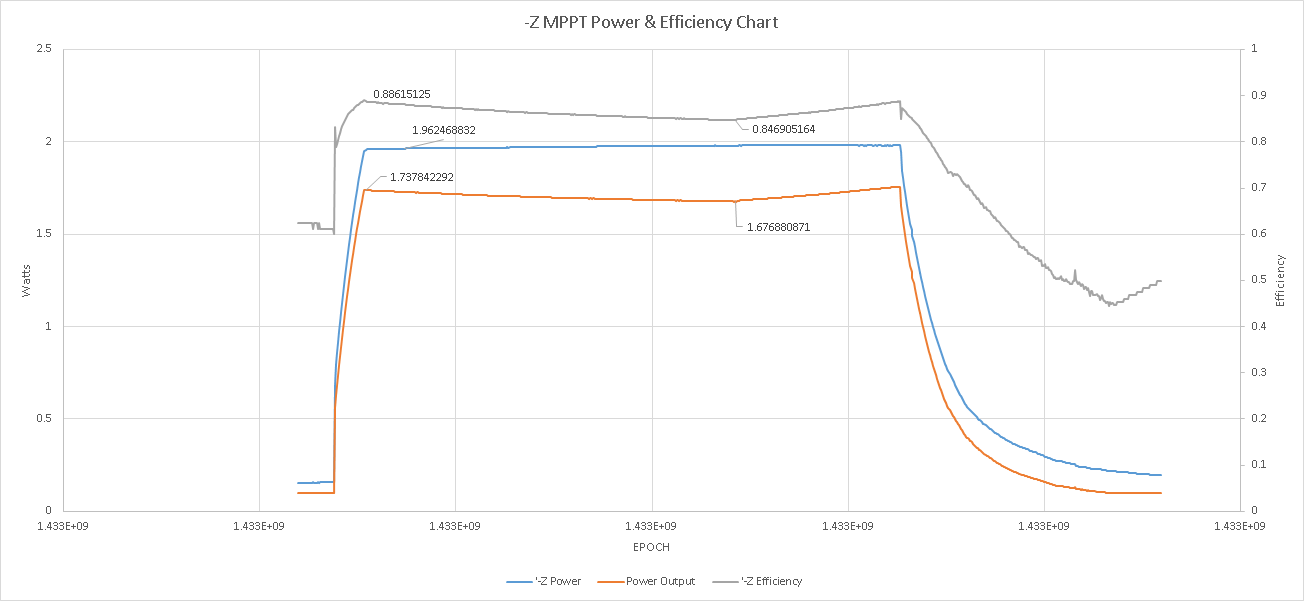
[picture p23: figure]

Figure 30: -Z panel operation showing solar panel power output, MPPT output power, and resulting efficiency over a super capacitor discharge test

## Oscilloscope Captures

To showcase some of the MPPT operations Figure 31 is an oscilloscope capture of an MPPT load test. Channel 1 (top) is the simulated solar panel voltage, Channel 2 (middle) is the output voltage, and Channel 3 (bottom) is the switching node of the buck converter. A 50mA constant current load was the steady state operation condition the test started in. This means the MPPT was actually in voltage regulation mode to begin the test. A 1A constant current transient was immediately placed onto the output of the MPPT (super capacitor) as a large load causing the capacitor voltage to sag slightly as shown in channel 2 when the test occurred about 100us from the left edge of the screen. It’s important to point out that MPPT output voltage droop is not critical as the battery will buffer the voltage transient in nominal operation. Please note this test is extremely unforgiving and unrealistic in orbit but a great example non-the-less.

Transitioning from voltage regulation mode into MPPT mode, the solar panel voltage dipped a bit below the maximum power point and then rose back up to maintain MPPT. Channel 3 clearly shows the duty cycle of the buck converter changing as the feedback loops maintain regulation. The switching node duty cycle is the important observation and absolute voltage of the switching node will track with the panel voltage as shown. Complete tradeoff of voltage regulation to MPPT regulation is observed in this oscilloscope capture. This event occurred in about 1ms from beginning to end which is more than sufficient for on-orbit performance since spacecraft rotation is much slower.

Figure 31: MPPT Operating with a charged super capacitor simulating a battery experiencing a load transient. Load was intense 50mA to 1A transient.

# Appendix

## Fox-1 Solar Panel Calculations

Fox-1 Solar Panel
PV Temp (C) | VOC (V) | VMPP (V) | IMPP (A) | PMPP (W)
-60 | 6.464 | 5.844 | 0.440 | 2.571
-55 | 6.399 | 5.779 | 0.440 | 2.543
-50 | 6.334 | 5.714 | 0.440 | 2.514
-45 | 6.269 | 5.649 | 0.440 | 2.486
-40 | 6.204 | 5.584 | 0.440 | 2.457
-35 | 6.139 | 5.519 | 0.440 | 2.428
-30 | 6.074 | 5.454 | 0.440 | 2.400
-25 | 6.009 | 5.389 | 0.440 | 2.371
-20 | 5.944 | 5.324 | 0.440 | 2.343
-15 | 5.879 | 5.259 | 0.440 | 2.314
-10 | 5.814 | 5.194 | 0.440 | 2.286
-5 | 5.749 | 5.129 | 0.440 | 2.257
0 | 5.684 | 5.064 | 0.440 | 2.228
5 | 5.619 | 4.999 | 0.440 | 2.200
10 | 5.554 | 4.934 | 0.440 | 2.171
15 | 5.489 | 4.869 | 0.440 | 2.143
20 | 5.424 | 4.804 | 0.440 | 2.114
25 | 5.359 | 4.739 | 0.440 | 2.086
28 | 5.320 | 4.700 | 0.440 | 2.068
30 | 5.294 | 4.674 | 0.440 | 2.057
35 | 5.229 | 4.609 | 0.440 | 2.028
40 | 5.164 | 4.544 | 0.440 | 2.000
45 | 5.099 | 4.479 | 0.440 | 1.971
50 | 5.034 | 4.414 | 0.440 | 1.943
55 | 4.969 | 4.349 | 0.440 | 1.914
60 | 4.904 | 4.284 | 0.440 | 1.886

Table 11: Estimated operating parameters of the Fox-1 solar panel using two Spectrolab UTJ cells in series

## Maximum Power Point Tracking Theory

Solar Panels convert the Sun’s energy into electrical power for use by Fox-1. Due to the high impedance nature of solar cells, the payload can drastically affect the amount of power extracted from the cells by changing the voltage of panels with current draw from them. There is a specific voltage at which the maximum amount of power may be extracted which is called the Maximum Power Point Voltage, MPPV. This voltage varies with temperature and solar irradiance. An MPPT follows the maximum power point as it moves due to environmental disturbances.

The standard view of solar cell performance is by that of a current-voltage curve or IV curve as shown in Figure 32 from the Spectrolab UTJ solar cells (http://www.spectrolab.com/DataSheets/cells/PV%20UTJ%20Cell%205-20-10.pdf) used on Fox-1. To understand how to obtain information from the chart start with the two extremes. An open-circuit conducts no current and will operate the solar cell at the maximum voltage of about 2.66V on the bottom right of the IV curve. As current drawn from the solar cell is increased by the payload, the operating point of the solar cell moves from right to left along the plotted line. Under a short circuit condition the solar cell shows zero volts of potential and deliver about 17.05 mA/cm² of solar cell area to the load.

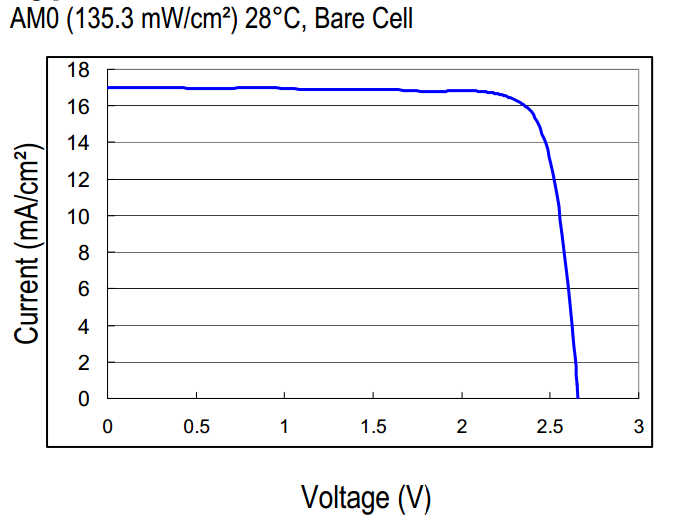
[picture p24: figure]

Figure 32: Spectrolab UTJ 28.3% efficiency solar cell IV curve

These two extremes both produce zero power in the ideal world.

Power=2.66 V ×0 A=0 Watts (open circuit) Power=0 V ×16.3(mA)/(cm^2)=0 Watts (short circuit)

The “knee” of the IV curve shown at about 2.35V on the x-axis is the maximum power point where the most energy can be extracted from the solar cell and delivered to the payload. Figure 33 shows example power curves and IV curves are as the values vary with temperature and irradiance of the solar cells. Notice how temperature is a huge contributor to changing the maximum power point.

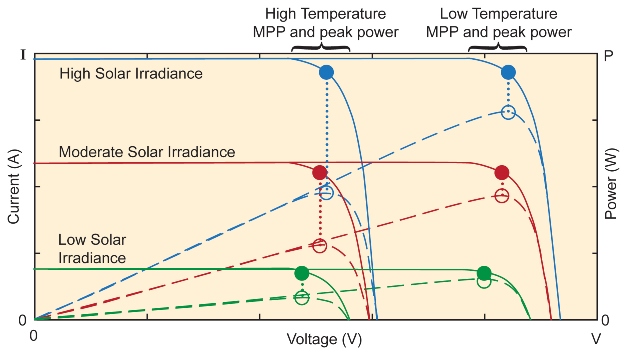
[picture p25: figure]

Figure 33: Solar panel MPPT versus temperature and irradiance changes. Image used from http://www.electronicproducts.com

A maximum Power Point Tracker is an intermediate circuit between the solar panels and the battery/satellite which isolates the source from the load in order to maintain the solar panel voltage at the MPPV. MPPTs are implemented with DC/DC converters and can be seen as impedance converters which match the high impedance of the solar panel (about 13Ω on Fox-1) to the payload which is usually much higher (low power needs) or much lower (high power needs) impedance. Used as an intermediate translator of impedances, the MPPT serves to decouple payload needs from solar panel operating point.

[^1] Bryce Salmi (KB1LQC), Brenton Salmi (KB1LQD), Ian MacKenzie (KB3OCF), Dan Corriero
[^2] http://cdn.intechopen.com/pdfs-wm/37984.pdf

AMSAT Fox-1 Maximum Power Point Tracker

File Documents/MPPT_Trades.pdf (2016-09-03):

# Fox-1 MPPT Trades

PSU V1.07 | ZSMP4523 – IC Solution | TL1454 – Fox 2 Style | MSP430 – Smart MPPT


Pros | Pros | Pros | Pros
Cons | Cons | Cons | Cons
- Already built · Simple, likely very reliable · Available for engineering model testing · Least schedule impact for PSU/MPPT team | · Super small · Extremely efficient (~95% at times) · Quick to implement for Fox-1 · Evaluation board available < $50
- Designed for super-capacitors 2.7V output · Unknown radiation tolerance · Overall reliability unknown
- PWM Controller works down to 3.6V · Modeling Fox-2 MPPT architecture from

Rochester Institute of Technology · Could be fairly efficient (non-synchronous) · Could be very efficient (synchronous) but

harder to implement, more PCB area · Stateless design (radiation friendly) · MOSFET driver included in IC · Likely requires a SEPIC converter which

has larger PCB area · May not fit six MPPTs on one board · One PWM loop likely unused · Not radiation tested · Rated for 0C to 70C · Is obsolete but offered by Mouser (low

quantity) · Potentially long MPPT design time

- Very small footprint compared to Fox-2 architecture. · Allows most flexibility in MPPT design

such as P&O method, maximum current · FRAM devices offered (radiation

tolerance) · Long-term triplication possible · Aerospace Industry uses MSP430s often · Uses state which is risky for radiation · Requires some extensive C firmware

programming · Overall system complexity increased · Potentially long MPPT design time · Uses LDO regulators which are inefficient · Likely a large hit to power budget · Likely reduced Fox-1 on-orbit operational

capability · Dumps excess voltage as heat

Bryce Salmi
4-5-2014

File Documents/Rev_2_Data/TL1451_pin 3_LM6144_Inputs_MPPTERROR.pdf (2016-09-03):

## 2K resistors into TL1451 pin 3


Channel 1 LM6144 Pin 8
Channel 2: TL1451 pin 3
Channel 3 LM6144 pin 9
Channel 4: LM6144 pin 10

1: -60C 3.3Vout load (no start)

2: -60C 50mA load

Inputs get pulled apart when no start happens

Wednesday, November 18, 2015 11:07 AM

AMSAT Page 1

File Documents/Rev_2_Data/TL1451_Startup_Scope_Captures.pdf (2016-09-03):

## 2K resistors into TL1451 pin 3

# TL1451 Startup Scope Captures


Channel 1 LM6144 Pin 8
Channel 2: TL1451 pin 3
Channel 3 LM6144 pin 7
Channel 4: Vin

0C into 3.3Vout Load (No Start)

0C Into 50mA Load

Wednesday, November 18, 2015 2:12 AM

AMSAT Page 1


-60C into 50mA load

-60C into 3.3Vout load (no start)

60C into 50mA load

60C into 3.3Vout load

## 2K resistors into TL1451 pin 4/5

Channel 1 LM6144 Pin 8
Channel 2: TL1451 pin 4/5
Channel 3 LM6144 pin 7
Channel 4: Vin

-60C into 50mA Load

-60C into 3.3Vout Load

0C into 3.3Vout Load

0C into 50mA Load

60C into 50mA Load

60C into 3.3Vout Load

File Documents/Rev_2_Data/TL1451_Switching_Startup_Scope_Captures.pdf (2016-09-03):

## 2K resistors into TL1451 pin 4/5

# TL1451 Switching Startup Scope Captures


Channel 1 LM6144 Pin 8
Channel 2: TL1451 pin 4/5
Channel 3 LM6144 pin 7
Channel 4: VSwitch

1: 0C into 3.3Vout

2: 0C into 50mA load

Wednesday, November 18, 2015 11:01 AM

AMSAT Page 1


3: 0C into 3.3Vout

## 2K resistors into TL1451 pin 3

Channel 1 LM6144 Pin 8
Channel 2: TL1451 pin 3
Channel 3 LM6144 pin 7
Channel 4: VSwitch

4: 0C int0 3.3Vout load

5: 0C into 50mA load

6: -60C into 3.3Vout load (no start)

7: -60C into 50mA load

8: -60C into 3.3Vout load (zoomed) no start

## 2K resistors into TL1451 pin 3

Channel 1 LM6144 Pin 8
Channel 2: TL1451 pin 3
Channel 3 LM6144 pin 7
Channel 4: Pin 5 of LT4413

9: -60C into 3.3Vout load (no start)

10: -60C into 50mA load

## 2K resistors into TL1451 pin 3, Ideal diode IN/OUT shorted

Channel 1 LM6144 Pin 8
Channel 2: TL1451 pin 3
Channel 3 LM6144 pin 7
Channel 4: Pin 5 of LT4413

11: -60C into 50mA load

12: -60C into 3.3Vout load

Conclusion
Does not look like the ideal diode or 2.5V reference (not scope captured)

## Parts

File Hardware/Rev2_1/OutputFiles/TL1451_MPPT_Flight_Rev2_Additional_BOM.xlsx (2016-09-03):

The Radio Amateur Satelite Corporation - AMSAT
Fox-1 Maximum Power Point Tracker | Additional Parts
Revision | 2 | Engineer | Bryce Salmi
Date | 2015-12-01 |  | KB1LQC
Reference Designator | Value | Quantity | Footprint | Tolerance/Rating | Manufacturer Part Number | Supplier Link | Note
Solar Panel Thermistors | 100 | 6 | R0805 | 1% | PTS080501B100RP100 | http://www.digikey.com/product-detail/en/PTS080501B100RP100/PTS0805100CT-ND/1666190 | Replace thermistors on solar cells with RTDs

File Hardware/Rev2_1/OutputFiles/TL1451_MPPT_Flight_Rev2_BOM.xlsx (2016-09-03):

The Radio Amateur Satelite Corporation - AMSAT
Fox-1 Maximum Power Point Tracker
Revision | 2.0 | Engineer | Bryce Salmi |  | Part Count | 421
Date | 2015-12-01 |  | KB1LQC |  | Line Items | 52
Reference Designator | Value | Quantity | Footprint | Tolerance/Rating | Manufacturer Part Number | Supplier Link
C12 C14 C78 C83 C42 C67 C72 C77 C82 C87 C88 C89 C95 C96 C102 C103 C109 C110 C116 C117 C123 C124 C127 | 1uF | 23 | C0402 | 16V | GRM155C81E105ME11D | http://www.digikey.com/product-search/en?pv252=42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
C125 C126 | 0.39uF | 2 | C0603 | 16V | GRM188R71C394KA88D | http://www.digikey.com/product-search/en?pv13=45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
C128 | 0.01uF | 1 | C0402 | 16V | GRM155R71C103KA01D | http://www.digikey.com/product-detail/en/GRM155R71C103KA01D/490-1313-6-ND/615368
C13 C17 C46 C51 C55 C58 C68 C73 C6 C60 C69 C74 C79 C84 C148 C151 C152 C153 C154 C155 | 1uF | 20 | C0603 | 16V | GRM188R7YA105KA12D | http://www.digikey.com/product-detail/en/GRM188R7YA105KA12D/490-10487-1-ND/5026405
C15 C16 C18 C1 C10 C11 C19 C28 C37 C3 C21 C30 C39 C48 C57 C8 C26 C35 C44 C53 C62 C64 C24 C65 C70 C75 C80 C85 C144 C129 C132 C135 C138 C141 C145 C149 C150 C156 C157 C158 C159 C160 C161 C162 C163 C164 C165 C166 C167 C168 C169 C170 C171 C172 C173 | 0.1uF | 55 | C0402 | 16V | GRM155R71C104KA88D | http://www.digikey.com/product-detail/en/GRM155R71C104KA88D/490-3261-1-ND/702802
C2 C20 C29 C38 C47 C56 | 220pF | 6 | C0402 | 16V, NPO/C0G | GRM1555C1H221FA01D | https://www.digikey.com/product-detail/en/GRM1555C1H221FA01D/490-10684-1-ND/5251421
C22 C91 C98 C105 C112 C119 C40 C93 C100 C107 C114 C121 | 820pF | 12 | C0402 | 50V | GRM155R71H821KA01D | http://www.digikey.com/product-detail/en/GRM155R71H821KA01D/490-3250-1-ND/702791
C130 C133 C136 C139 C142 C146 C131 C134 C137 C140 C143 C147 | DNP | 12 | C0402 | 16V | DNP
C4 C90 C97 C104 C111 C118 C31 C92 C99 C106 C113 C120 | 0.012uF | 12 | C0402 | 16V | GRM155R71C123KA01D | http://www.digikey.com/product-detail/en/GRM155R71C123KA01D/490-3255-1-ND/702796
C42 C67 C72 C77 C82 C87 | 1uF | 6 | C0402 | 35V | C1005X5R1V105K050BC | https://www.digikey.com/product-detail/en/C1005X5R1V105K050BC/445-9073-1-ND/3648734
C5 C23 C32 C41 C50 C59 C7 C25 C34 C43 C52 C61 | 47uF | 12 | C1210 | 16V | GRM32ER61C476KE15K | http://www.digikey.com/product-search/en?pv3=3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
C9 C27 C36 C45 C54 C63 C49 C94 C101 C108 C115 C122 | 0.015uF | 12 | C0402 | 16V | GRM155R71C153KA01D | http://www.digikey.com/product-detail/en/GRM155R71C153KA01D/490-1314-1-ND/587932
D1 D2 D3 D4 D5 D6 | PMEG3020EP | 6 | SOD128 |  | PMEG3020EP,115 | http://www.digikey.com/product-detail/en/PMEG3020EP,115/568-7402-1-ND/2697503
D7 D9 D11 D13 D15 D17 | SDM10U45-7 | 6 | SOD523 |  | SDM10U45-7 | http://www.digikey.com/product-search/en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
R1 R3 R4 R17 R20 R24 | MPMT4001AT1 | 6 | SOT23 |  | MPMT4001AT1 | https://www.digikey.com/product-search/en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
F2 F3 F4 | NFL21SP106X1C3D | 3 | NFL21SP |  | NFL21SP106X1C3D | http://www.digikey.com/product-detail/en/NFL21SP106X1C3D/490-4016-1-ND/1016276
G1 | AMSAT_LOGO_SMALL | 1 | AMSAT_Logo_Small |  | DNP
G2 | RIT_LOGO_SMALL | 1 | RIT_Logo_Small |  | DNP
L1 L2 L3 L4 L5 L6 | 22uH | 6 | CLF7045T | CLF7045T-220M-H | CLF7045T-220M-H | http://www.digikey.com/product-search/en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
L7 | 10uH | 1 | SLF6045 | SLF6045T-100M1R6-3PF | SLF6045T-100M1R6-3PF | http://www.digikey.com/product-search/en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
P1 P2 P3 P4 | CONN_5X2 | 4 | MEC1-105-02-L-D-NP-A |  | DNP
P5 | QSH-030-01-X-D-A | 1 | QSH-030-01-L-D-A |  | QSH-030-01-L-D-A | http://www.digikey.com/product-detail/en/QSH-030-01-L-D-A/SAM8180-ND/1106524
P6 | QTH-030-02-X-D-A | 1 | QTH-030-02-L-D-A |  | QTH-030-02-L-D-A | http://www.digikey.com/product-detail/en/QTH-030-02-L-D-A/SAM8186-ND/1106530
P7 P8 P9 P10 | CONN_1 | 4 | FOX_Mounting_Hole |  | DNP
Q1 Q5 Q9 Q13 Q14 Q15 | DMP2066LDM-7 | 6 | SOT26 |  | DMP2066LDM-7 | http://www.digikey.com/product-search/en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
Q2 Q3 Q6 Q7 Q10 Q11 | MMDT2227M | 6 | SOT26 |  | MMDT2227M-7 | http://www.digikey.com/product-detail/en/MMDT2227M-7/MMDT2227MDICT-ND/1099164
Q4 Q8 Q12 Q16 Q17 Q18 | 2N7002K | 6 | SOT23 |  | 2N7002K | http://www.digikey.com/product-detail/en/2N7002K/2N7002KCT-ND/2060375
R10 R49 R78 R107 R136 R165 | 6.04 | 6 | R0603 | 0.01 | CRCW06036R04FKEA | http://www.digikey.com/product-search/en?s=18616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
R11 R50 R79 R108 R137 R166 | 2K | 6 | R0402 | 0.001 | ERA-2AEB202X | http://www.digikey.com/product-search/en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
R12 R51 R80 R109 R138 R167 R13 R52 R81 R110 R139 R168 R16 R55 R84 R113 R142 R171 R19 R58 R87 R116 R145 R174 | 249K | 24 | R0402 | 0.001 | ERJ-2RKF2493X | http://www.digikey.com/product-search/en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
R14 R53 R82 R111 R140 R169 | 100 | 6 | R0402 | 0.001 | MCS0402MD1000BE100 | http://www.digikey.com/product-search/en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
R15 R54 R83 R112 R141 R170 | 2.49K | 6 | R0402 | 0.001 | ERA-2AEB2491X | http://www.digikey.com/product-search/en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
R18 R57 R86 R115 R144 R173 | 27K | 6 | R0402 | 0.001 | ERA-2AEB273X | http://www.digikey.com/product-detail/en/ERA-2AEB273X/P27KDCCT-ND/1706217
R187 R202 R204 R206 R208 R210 R212 | 30.1K | 7 | R0402 | 0.001 | ERA-2AEB3012X | http://www.digikey.com/product-search/en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
R188 | 40.2K | 1 | R0402 | 0.001 | ERA-2AEB4022X | http://www.digikey.com/product-search/en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
R2 R48 R105 R162 R219 R228 R6 R70 R106 R163 R220 R229 | 261 | 12 | R0402 | 0.001 | ERA-2AEB2610X | http://www.digikey.com/product-detail/en/ERA-2AEB2610X/P261DCCT-ND/3063748
R201 R203 R205 R207 R209 R211 | 51.1K | 6 | R0402 | 0.001 | ERA-2AEB5112X | http://www.digikey.com/product-search/en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
R21 R60 R89 R118 R147 R176 R26 R65 R94 R123 R152 R181 R9 R76 R133 R214 R223 R232 | 3.32K | 18 | R0402 | 0.001 | ERA-2AEB3321X | http://www.digikey.com/product-detail/en/ERA-2AEB3321X/P3.32KDCCT-ND/3063779
R22 R185 | 0.051 | 2 | R0603 | 0.01 | UCR03EVPFSR051 | http://www.digikey.com/product-search/en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
R23 R62 R91 R120 R149 R178 | 24.3K | 6 | R0402 | 0.001 | ERA-2AEB2432X | http://www.digikey.com/product-detail/en/ERA-2AEB2432X/P24.3KDCCT-ND/3063741
R25 R64 R93 R122 R151 R180 | 2.4K | 6 | R0402 | 0.001 | ERA-2AEB242X | http://www.digikey.com/product-detail/en/ERA-2AEB242X/P2.4KDCCT-ND/1706192
R27 R66 R95 R124 R153 R182 R7 R74 R128 R164 R221 R230 | 4.75K | 12 | R0402 | 0.001 | ERA-2AEB4751X | http://www.digikey.com/product-search/en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
R29 R68 R97 R126 R155 R184 | 6.49K | 6 | R0402 | 0.001 | ERA-2AEB6491X | http://www.digikey.com/product-detail/en/ERA-2AEB6491X/P6.49KDCCT-ND/3063876
R30 R31 R32 R33 R34 R35 R36 R40 R41 R42 R43 R45 R46 R56 R59 R189 R191 R193 R195 R197 R199 R190 R192 R194 R196 R198 R200 R28 R67 R104 R154 R183 R227 | 10K | 33 | R0402 | 0.001 | ERA-2AEB103X | http://www.digikey.com/product-search/en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
R37 | 71.5K | 1 | R0402 | 0.001 | ERA-2AEB7152X | http://www.digikey.com/product-search/en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
R38 | 330 | 1 | R0402 | 0.001 | ERA-2AEB331X | http://www.digikey.com/product-detail/en/ERA-2AEB331X/P330DCCT-ND/1706171
R39 | 9.09K | 1 | R0402 | 0.01 | ERA-2AEB9091X | http://www.digikey.com/product-search/en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
R47 R96 R125 R161 R218 R236 | 47K | 6 | R0402 | 0.01 | ERJ-2RKF4702X | https://www.digikey.com/product-detail/en/ERJ-2RKF4702X/P47.0KLCT-ND/1746693
R5 R44 R73 R102 R131 R160 | 4.99K | 6 | R0402 | 0.001 | ERJ-2RKF4991X | https://www.digikey.com/product-detail/en/ERJ-2RKF4991X/P4.99KLCT-ND/194389
R61 R71 R85 R92 R100 R114 | 205K | 6 | R0402 | 0.001 | ERJ-2RKF2053X | http://www.digikey.com/product-search/en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
R63 R72 R88 R98 R101 R117 R69 R77 R90 R99 R103 R119 | DNP | 12 | R0402 | 0.001 | DNP
R8 R75 R132 R213 R222 R231 | 1.54K | 6 | R0402 | 0.001 | ERA-2AEB1541X | http://www.digikey.com/product-detail/en/ERA-2AEB1541X/P1.54KDCCT-ND/3063686
TH1 | NTCS0603E3103FMT | 1 | R0603 |  | NTCS0603E3103FMT | http://www.digikey.com/product-detail/en/NTCS0603E3103FMT/BC2472CT-ND/2230853
U1 U8 U11 U14 U17 U20 | LTC4411 | 6 | TSOT23-5 |  | LTC4411ES5#TRMPBF | http://www.digikey.com/product-detail/en/LTC4411ES5%23TRMPBF/LTC4411ES5%23TRMPBFCT-ND/1754256
U2 U9 U12 U15 U18 U21 | TL1451A | 6 | PW16 |  | TL1451ACPWR | http://www.digikey.com/product-detail/en/TL1451ACPWR/296-10135-1-ND/380751
U23 | INA195 | 1 | SOT23-5 |  | INA195AIDBVR | http://www.digikey.com/product-detail/en/INA195AIDBVR/296-26067-1-ND/2254841
U3 U10 U13 U16 U19 U22 | LM6144A | 6 | SO14 |  | LM6144AIM/NOPB | http://www.digikey.com/product-detail/en/LM6144AIM%2FNOPB/LM6144AIM%2FNOPB-ND/367289
U5 U7 | ADS7828 | 2 | PW16 |  | ADS7828E/250 | http://www.digikey.com/product-detail/en/ADS7828E%2F250/296-12402-1-ND/417222

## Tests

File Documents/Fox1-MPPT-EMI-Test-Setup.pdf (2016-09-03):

The Radio Amateur Satellite Corporation | AMSAT

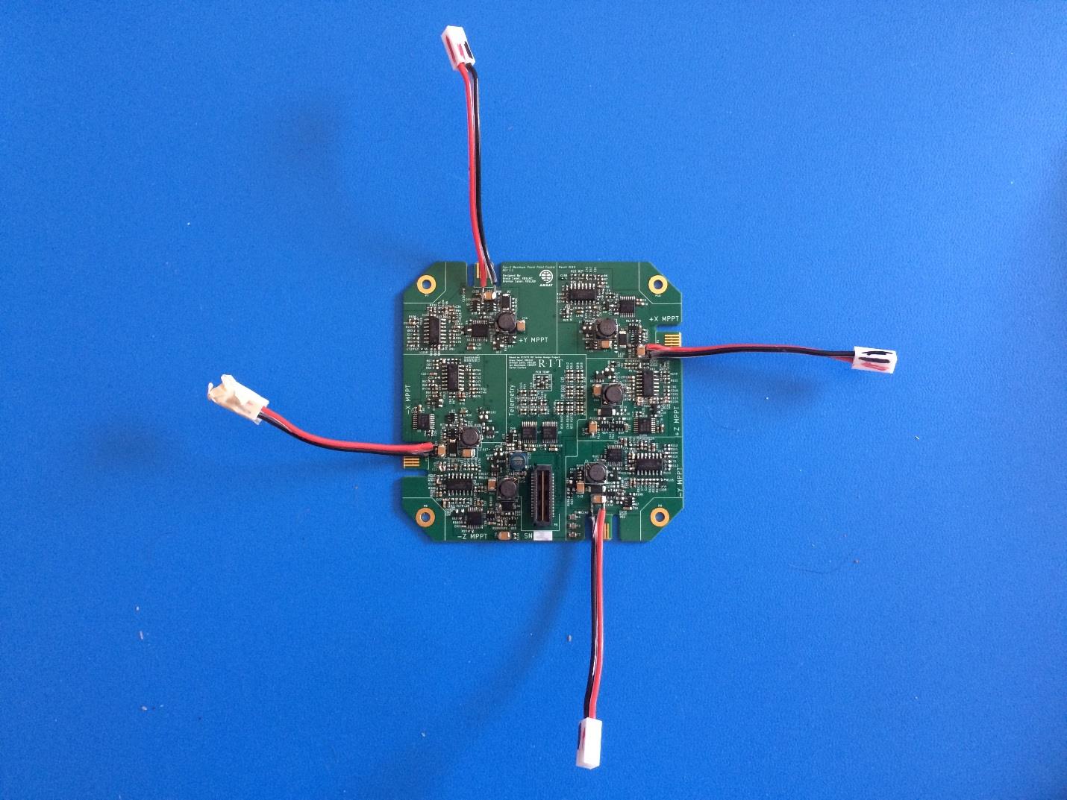
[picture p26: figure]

April 28, 2015 | Fox-1 MPPT EMI Test Setup | 1

# Fox-1 Maximum Power Point Tracker EMI Testing

MPPT Serial Number | 2

Bryce Salmi, KB1LQC

## Contents

## Introduction

The Fox-1 Maximum Power Point Tracker, MPPT, is an analog solar panel interface which maximizes the power extracted from two series connected Spectrolab UTJ solar cells. It will force the solar panel, or simulator, to operate at a constant voltage predicted to be the maximum power point only if maximum power is being requested by the load. Otherwise, the panel voltage is allowed to rise to the appropriate voltage for the given load and temperature. Each MPPT PCB has six individual channels which can operate in two modes being output voltage regulation and maximum power point tracking.

This document will overview basic hardware setup for use with items sent to Dan Habecker, W9EQ, for RFI sniffing. It also serves as a basic document for using the MPPT in a testing environment with common test gear associated with DC/DC converter and MPPT testing.

## MPPT Test Setup

Hardware required for testing the MPPT include

- Fox-1 Maximum Power Point Tracker Rev 1.1 PCBA
- AMSAT Fox-1 Motherboard
- Semtec connector harness adapter (Optional)
- Associated motherboard harness
- Solar Panels/Simulation Hardware (At least one)
- Solar Panels
- LM723 Solar Simulator
- Solar Panel Series Resistance Simulator
- Input and output cables./harnesses
- Battery/Supercapacitors
- Load
- Resistive or active

### Equipment Shipped

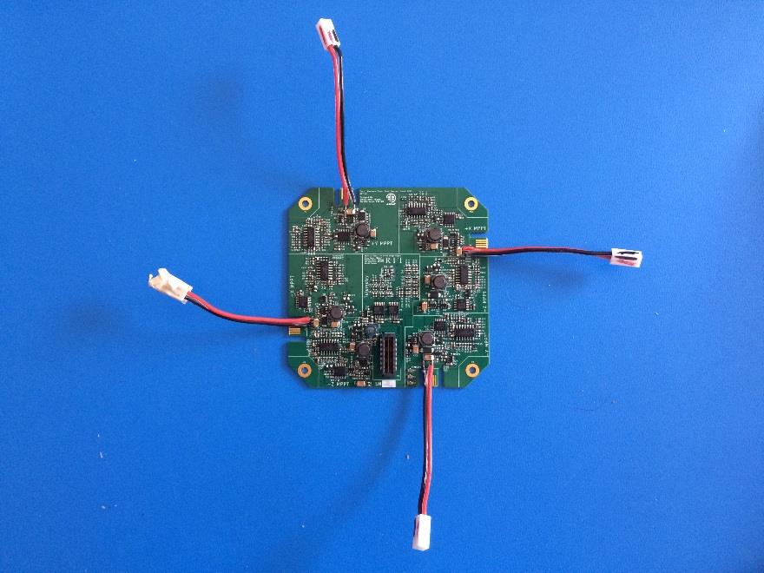
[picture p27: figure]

Figure 1 Fox-1 Maximum Power Point Tracker Rev 1.1 with test pigtails soldered onto PCBA (QTY: 1)

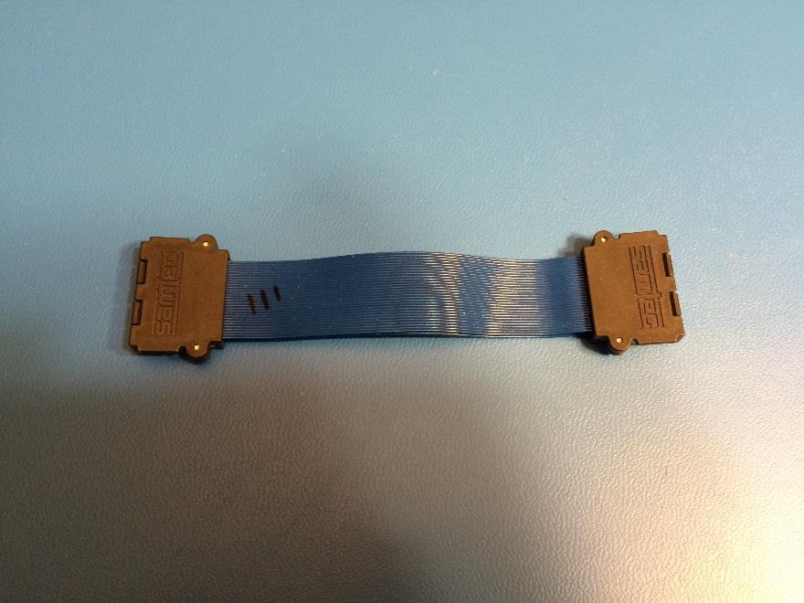
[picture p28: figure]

Figure 2 Semtec connector adapter cable (QTY: 1)

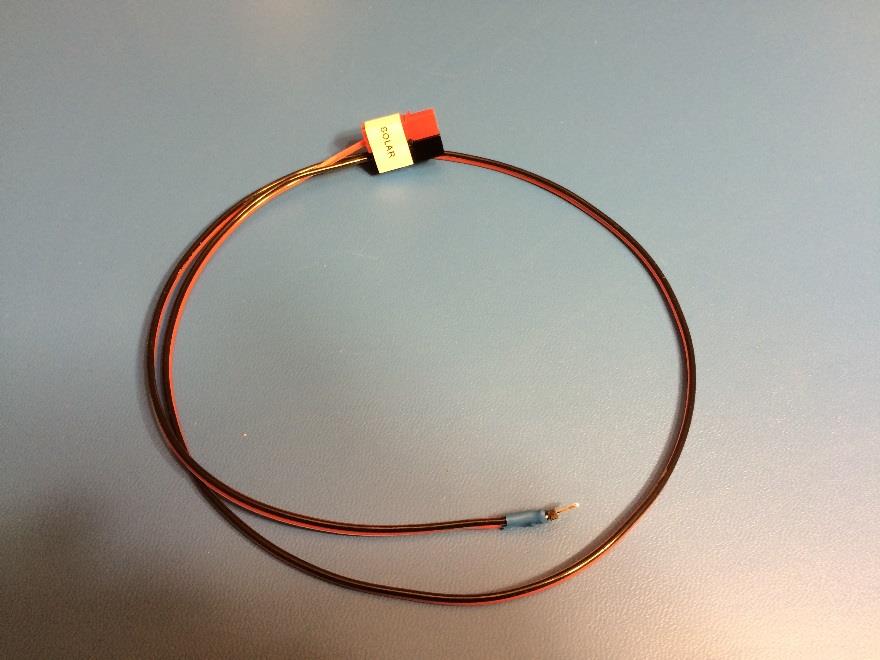
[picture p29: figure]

Figure 3 Solar panel pigtail to Anderson power pole cable (QTY: 2)

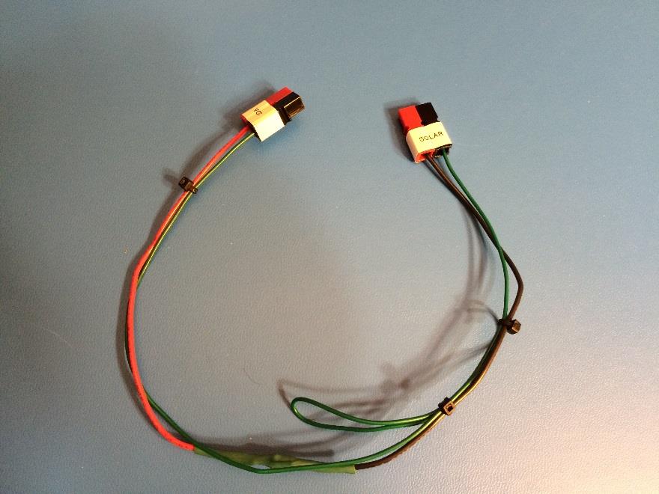
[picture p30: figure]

Figure 4 Solar panel series resistance simulator. Resistance = 1.4Ω (QTY: 1)

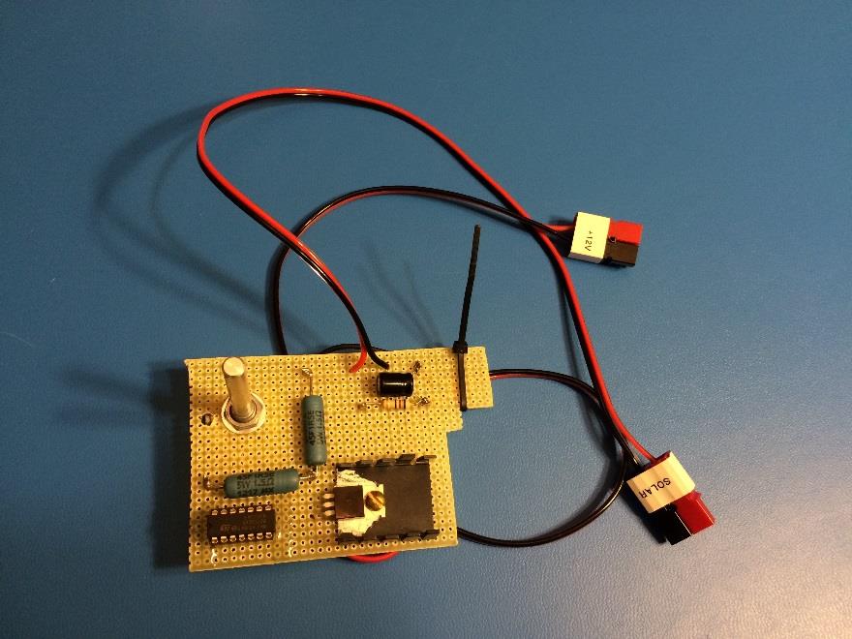
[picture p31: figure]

Figure 5 LM723 Solar Simulator (QTY: 1)

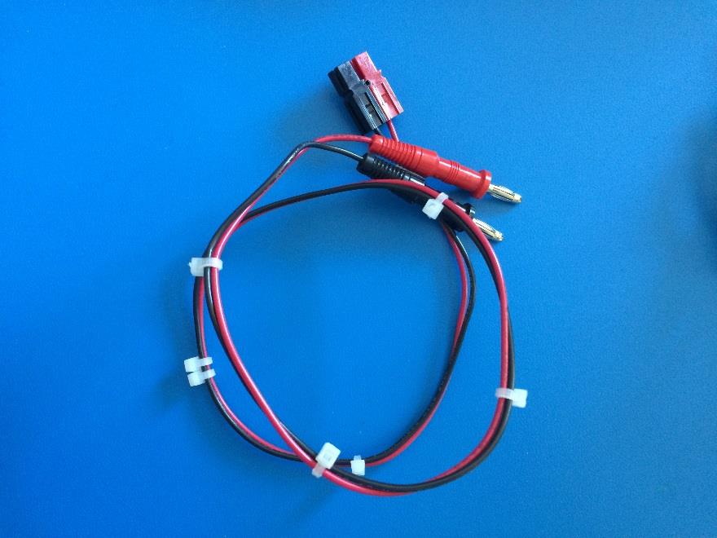
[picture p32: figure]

Figure 6 Anderson power pole to banana plug cable (QTY: 2)

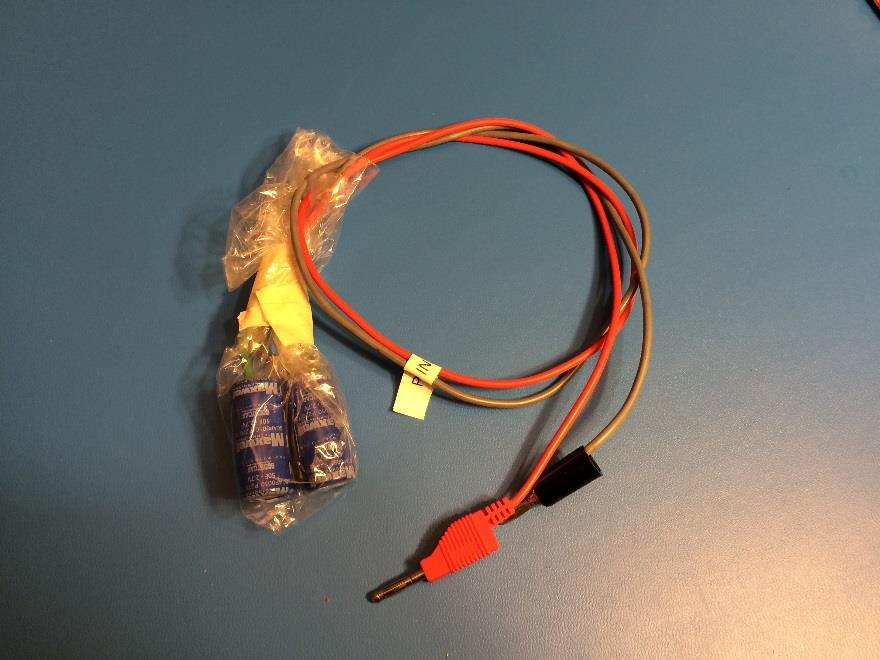
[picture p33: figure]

Figure 7 2.5 Farad 5.4V Supercapacitor with banana plugs

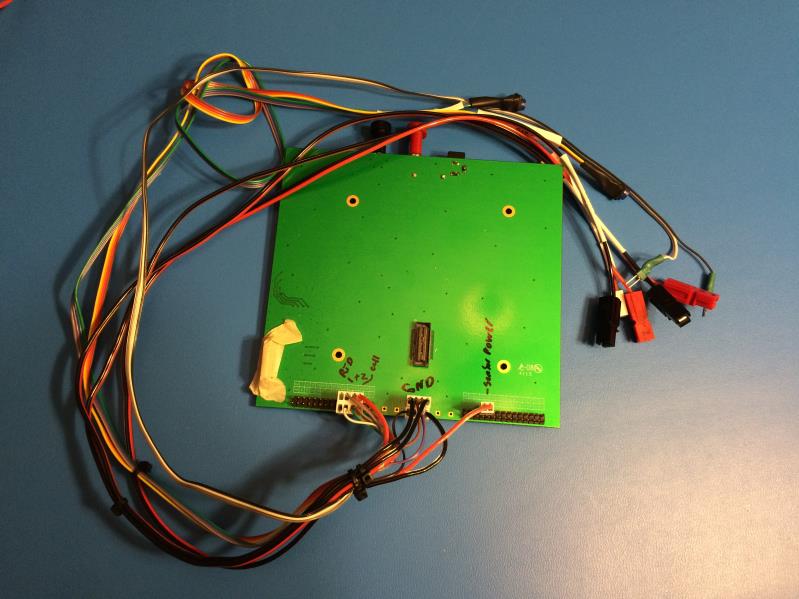
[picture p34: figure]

Figure 8 AMSAT Fox-1 motherboard with MPPT harnessing

Items Not Shown
- Anderson power pole to wire terminal cables (QTY: 2)

## MPPT Test Setup

Figure 9 General test setup for using the MPPT

The MPPT only operates correctly with a power source that looks like a solar panel. Now, solar panels have current-voltage (IV) curves but the MPPT simply requires that it is able to change the input voltage with a change of input current.

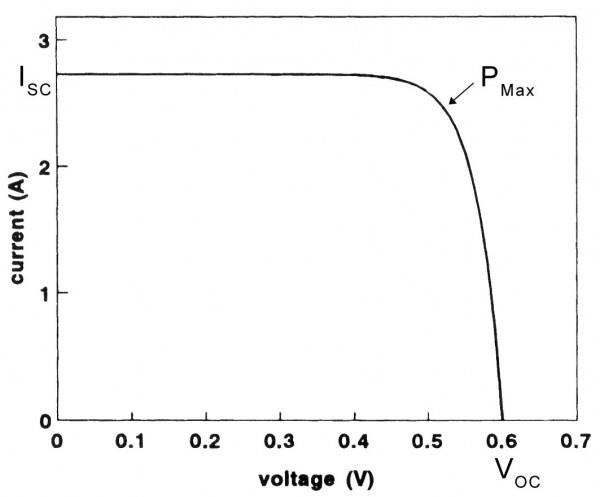
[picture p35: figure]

Figure 10 Solar panel IV curve for reference only

Solar panels have a series resistance that is the easiest to mimic. This is essentially the slope of the line in Figure 10 from right to left before the “knee” of the curve around 0.55V in the example IV curve. This can be confusing, please keep in mind that a solar panel sitting in the sun attached to no load is all the way right in Figure 10 at VOC and a solar panel that is shorting its output wires is all the way left sitting at ISC. As load increases on the IV curve above the operating point moves from right to left.

### Resistive Solar Simulation

A simple resistor combined with the correct power supply voltage will allow the MPPT to operate along a linear voltage drop across its input. Carefully setting up the voltage and resistance will allow the MPPT to reach the appropriate current input at the exact point it hits the voltage it wants to regulate the input to as shown in Figure 11.


Figure 11 Example IV curve with a red resistive voltage drop line the MPPT will follow right to left as load is increased

An example 0°C operating point for solar simulation is show in Table 1. To properly reach the 5.064V maximum power point voltage (3% tolerance) at the correct 440mA current a 1.4Ω series resistance will require an open circuit voltage of 5.68V. Therefore setting a bench-top power supply to 5.68V and then attaching the resistive solar simulator, Fox-1 MPPT, and an output load will result in the test setup following a linear line all the way to the maximum power point voltage. This will deliver about 2.228W into the input of the MPPT.

Connection to the MPPT is made through Anderson power poles directly to the Fox-1 motherboard harness and/or the Anderson power pole to 0.100” pigtail cables.

0°C Resistive Simulation Values

VOC | RSeries | VMPP | IMPP | PMPP
5.680 V | 1.400 Ω | 5.064 V | 0.440 A | 2.228 W
Table 1 Operating values for a 0°C resistive solar simulation

Figure 12 Example block diagram of a MPPT test using the resistive method of solar simulation

VOC = VMPP + (IMPP × RSeries) = 5.064V + (0.440A × 1.4Ω) = 5.68V

More simulation settings for the resistive simulator can be found in MPPT_Expected_Voltages.xlxs. (http://amsatfox.org/repos/Power/EngineeringDocs/MPPT_Expected_Voltages_Fox-1.xlsx)

### LM723 Solar Simulation

The LM723 (http://www.ti.com/lit/ds/symlink/lm723.pdf) is a voltage regulator and is used as a simple IV curve tracer. A pass transistor allows > 100mA currents to be sourced from it. A basic operational overview is that the regulator is set to regulate to the intended open circuit voltage adjusted for the slope of the IV curve it is tracing (which differs from resistive methods due to different series resistance). As the load is increased the voltage will drop at the input of the MPPT until VMPP is reached or the LM723 current limit is hit. Once the LM723 current limit is reached (about 410mA) the simulator drops almost all the voltage from the power supply and the MPPT input voltage crashes towards 0V. This simulates a very basic IV curve.

VOC is adjusted with the potentiometer on the simulator while the power supply voltage should be sufficiently higher than the VOC to account for dropout. Values for the simulator are shown in Table 2 and a block diagram of the test setup with example voltages are shown in Figure 13. Connection to the MPPT is made through Anderson power poles directly to the Fox-1 motherboard harness and/or the Anderson power pole to 0.100” pigtail cables.

| 0°C LM723 Simulation Values
VOC | | RSeries | | VMPP | | IMPP | | PMPP
| 5.684 V | | 0.000 Ω | | 5.064 V | | 0.410 A | | 2.076 W
Table 2 The LM723 solar simulator 0°C operation values

Figure 13 MPPT test setup with the LM723 simulator

More simulation settings for the LM723 simulator can be found in MPPT_Expected_Voltages.xlxs. (http://amsatfox.org/repos/Power/EngineeringDocs/MPPT_Expected_Voltages_Fox-1.xlsx)

### MPPT Load

A load, resistive or active, must be placed on the output of the AMSAT Fox-1 Motherboard by attaching to the banana plugs shown in Figure 8. Please note that by the definition of an MPPT output voltage will plummet once maximum input power is achieved. This is conservation of power as power in = power out – inefficiency and if the load current keeps increasing then the voltage must decrease! A supercapacitor or battery in parallel with the output will stabilize the voltage under load causing more flight-like conditions.

## Fox-1 Maximum Power Point Tracker Operation

### MPPT SN2 Hardware

The serial number 2 PCB sent has 5 MPPTs on it that should be used. One MPPT, X- panel, works but requires a minimum load of 50mA or else the output will climb to the solar panel voltage (6V or so). Technically this is proper operation as DC/DC converters have a hard time regulating output voltage below a minimum current as they move into discontinuous conduction mode (DCM). I designed this MPPT for 50mA minimum load. However, the MPPTs should all operate fine without the minimum load so this is an open issue I’m investigating to make it easy on the integration team. I’ve taped over the –X Panel pigtail for now, please do not use it unless you provide the minimum load, especially with the supercaps as they could explode if you let them charge > 5.4V.

A bottom QSH connector is not present as soldering was not successful. Please use the Semtech cable adapter shown in Figure 2 if you want to access the top of the PCB while operating the MPPT with the PCB connected to the motherboard.

### Connecting Solar Power

The +Z and –Z MPPT inputs are achieved through the QSH/QTH connectors and therefore there are two Anderson power poles for these MPPTs in the AMSAT motherboard harness shown in Figure 8. The +X, -Y, and +Y MPPTs are powered through the pigtails near each Semtec PCB edge MEC connector in Figure 1. Please be extremely careful about not reverse polarizing the MPPTs with the 0.100” connector pigtails as this will likely damage the channel. Appropriate adapters for the connections have been provided, including wire terminal to Anderson power pole cables for the power supplies and load.

Multiple MPPT Operation Connection
When operating multiple MPPT channels simultaneously please keep in-mind that the PCB was designed for no more than two full power MPPTs operating at once. In orbit, one panel will be in direct sunlight while several other panels will be in indirect sunlight, three maximum at one time. Therefore, do not operate the MPPT with more than two full powered solar simulators.

The LM723 solar simulator needs a different voltage than the VOC power supply requirements of the resistive simulation method. This means that a separate power supply should be used for the LM723 and resistive simulators that provides a nominal 12V to the LM723 simulator and VOC to the resistor.

### MPPT SN2 Solar Panel RTD Setting

The SN2 MPPT channels require a resistance in place of the RTDs (http://en.wikipedia.org/wiki/Resistance_thermometer) used to measure each solar panel temperature. The MPPT was designed for PT100 RTDs which are 100Ω at 0°C. Therefore the –X, +X, -Y, and +Y channels have been hardware set to 100Ω with resistors soldered to the PCB. This cannot easily be changed. However, the –Z and +Z MPPT channels connect to potentiometers in the Fox-1 motherboard harness and can be varied over at least 74Ω to 124 Ω. When using 0C voltages as described above, please make sure the –Z and +Z potentiometers are set to 100Ω! These voltages are easily accessible on the Motherboard 0.100” connector pins for the RTDs.

RTDs are driven with 1mA so 100mV across the resistors = 100Ω

### Proper Operation of Fox-1 MPPT

The MPPT was designed for certain output conditions as shown in Table 3. The only valid voltage range is 4.2V to 3.3V. If the load is increased enough to bring the output voltage below 3.3V the results are no longer valid and MPPT operation is outside its design range. 1A can be sourced from the MPPT output when operating in combined dual panel operation. The minimum current is indicated as a design limit for guaranteed output voltage regulation. It should be noted that most MPPT channels don’t need this minimum current.

| Fox-1 MPPT Outputs
Vout Max | | Vout Min | | IOut Max | | IOut Min
| 4.200 V | | 3.300 V | | 1.000 A | | 0.050 A
Table 3 Output voltage and current values for valid operation

### Fox-1 MPPT Operational Modes

Voltage Regulation
When the load is light on the MPPT the output voltage will be regulated to no more than 4.2V. The solar panel voltage is allowed to rise until it reaches the open circuit voltage. Once the current in the solar panel reaches its designed maximum power point (440mA for resistive method or 410mA for LM723) the operational modes will switch from voltage regulation (regulating the output voltage only) and into MPPT (regulate the input voltage only).

Due to I²R losses the output voltage of the MPPT will linearly droop with increasing load up until the IMPP. Rest-assured the output capacitor of each MPPT is a rock-solid 4.20V. Durin this time the input solar panel voltage will be dropping with increased load.

Maximum Power Point Tracking
Once the load is heavy enough the MPPT switches off operating modes and the output voltage begins to fall out of regulation while the input solar panel voltage remains at the VMPP. The output power will remain the same (minus losses) while the current increases to the load but the voltage decreases. Do not increase the load such that the output voltage drops below 3.3V.

### Output Supercapacitor/Battery use

The output voltage can be held higher with increasing load by using a battery or supercapacitors. This increases efficiency as the voltage on the output stay high with increasing power. Be careful, supercapacitors will stay charged for a very long time and it’s important to discharge then when complete.

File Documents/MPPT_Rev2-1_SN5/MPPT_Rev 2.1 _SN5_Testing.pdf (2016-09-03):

## +X MPPT

- -60C Panel Simulator setting
- VOC = 6.83V
- Vrtd = 76mV +- 1mV
- Vload = 50mA
Vout | 4.290 | 4.3V
Vrtd | .0761
Vtemp | 1.404 | 0.0761*(-8.14228)+2.0523=1.43, low but OK
Vref | 2.474 | Low but OK

### -60C Voltage Regulation Check

### -60C MPPT Check

- -60C Panel Simulator setting
- VOC = 6.83V
- Vrtd = 76mV +- 1mV
- Vout Supercapacitor = 3.3V
Vpanel | 5.76 | 5.8V
Iin | ~0.440 | 440mA
Vtemp | 1.404
Some sagging of Vtemp when in MPPT

PASS

- +60C Panel Simulator setting
- VOC = 5.27V
- Vrtd = 124mV
- Vload = 50mA
Vout | 4.29 | 4.3V
Vrtd | 0.1237
Vtemp | 1.02 | 0.1237*(-8.14228)+2.0523=1.0451 Low but seems OK
Vref | 2.474 | Low but OK

### +60C Voltage Regulation Check

Testing with the solar simulator (LM713) I need to set the voltage at the solar cell (open circuit) to the MPPV + Vrslope which compensates for the resistance in the LM723 circuit. This means that at the MPP current I've dropped exactly enough voltage to actually be operating at the MPPV. While This isn't causing the MPPT to operate it does effectively simulate the correct amount of power through my board.

•

- ALL TESTS PERFORMED WITH THE BOTTOM SEMTEC BUS CONNECTOR CONNECTED TO MOTHERBOARD UNLESS OTHERWISE SPECIFIED, TOP BUS CONNECTOR NOT VERIFIED OTHERWISE

# MPPT Rev 2.1 | SN5

Tuesday, April 12, 2016 10:41 PM

AMSAT Page 1

### +60C MPPT Check

- +60C Panel Simulator setting
- VOC = 5.27V
- Vrtd = 124mV
- Vout Supercapacitor = 3.5V
Vpanel | 4.11 | 4.3… Hmm pretty low
Iin | ~0.44 | 440mA

PASS

VREF
MPPT ISOLATION
TL1251 Fsw -60C | 480.7KHz
TL1451Fsw 60C | 502.9 KHz
Scope Capture -60C | Oscillator MPPT | Quickprint2
Scope Capture -60C | SW Node MPPT | Quickprint1
Scope Capture +60C | SWNode MPPT | Quickprint 3

### MISC Checks

## -X MPPT

- -60C Panel Simulator setting
- VOC = 6.83V
- Vrtd = 76mV +- 1mV
- Vload = 50mA
Vout | 4.29 | 4.3V
Vrtd | 0.0764
Vtemp | 1.407 | 0.0764*(-8.14228)+2.0523=1.43023, low but OK
Vref | 2.472 | Low but OK

### -60C Voltage Regulation Check

### -60C MPPT Check

- -60C Panel Simulator setting
- VOC = 6.83V
- Vrtd = 76mV +- 1mV
- Vout Supercapacitor = 3.3V
Vpanel | 5.75 | 5.8V
Iin | ~0.44 | 440mA
Vtemp | 1.402
Some sagging of Vtemp when in MPPT

PASS

- +60C Panel Simulator setting
- VOC = 5.27V
- Vrtd = 124mV
- No Supercapacitor, Vload = 50mA
Vout | 4.29 | 4.3V (at Cout)
Vrtd | 124.2
Vtemp | 1.022 | 0.1242*(-8.14228)+2.0523=1.04103 Low but seems OK
Vref | 2.472 | Low but OK

### +60C Voltage Regulation Check

### +60C MPPT Check

- +60C Panel Simulator setting
- VOC = 5.27V
- Vrtd = 124mV
- Vout Supercapacitor = 3.5V
Vpanel | 4.18 | 4.3… Hmm low
Iin | ~0.440 | 440mA

PASS

VREF
MPPT ISOLATION
TL1251 Fsw -60C | 467.0KHz
TL1451Fsw 60C | 467.7 KHz
Scope Capture -60C | Oscillator MPPT | Quickprint7
Scope Capture -60C | SW Node MPPT | Quickprint6
Scope Capture +60C | SWNode MPPT | Quickprint5

### MISC Checks

## +Y MPPT

- -60C Panel Simulator setting
- VOC = 6.83V
- Vrtd = 76mV +- 1mV
- Vload = 50mA
Vout | 4.29 | 4.3V
Vrtd | .0752
Vtemp | 1.414 | 0.0752*(-8.14228)+2.0523=1.44, low but OK
Vref | 2.475 | Low but OK

### -60C Voltage Regulation Check

### -60C MPPT Check

- -60C Panel Simulator setting
- VOC = 6.83V
- Vrtd = 76mV +- 1mV
- Vout Supercapacitor = 3.3V
Vpanel | 5.78 | 5.8V
Iin | 0.44 | 440mA
Vtemp | 1.408
Some sagging of Vtemp when in MPPT

PASS

- +60C Panel Simulator setting
- VOC = 5.27V
- Vrtd = 124mV
- No Supercapacitor, Vload = 50mA
Vout | 4.29 | 4.3V
Vrtd | .1243
Vtemp | 1.018 | 0.1243*(-8.14228)+2.0523=1.04021 Low but seems OK
Vref | 2.475 | Low but OK

### +60C Voltage Regulation Check

### +60C MPPT Check

- +60C Panel Simulator setting
- VOC = 5.27V
- Vrtd = 124mV
- Vout Supercapacitor = 3.5V
Vpanel | 4.16 | 4.3… Hmm pretty low
Iin | ~0.44 | 440mA

PASS

VREF
MPPT ISOLATION
TL1251 Fsw -60C | 475.4KHz
Scope Capture -60C | Oscillator MPPT | Quickprint12
Scope Capture -60C | SW Node MPPT | Quickprint11
Scope Capture +60C | SWNode MPPT | Quickprint10

### MISC Checks

## -Y MPPT

- -60C Panel Simulator setting
- VOC = 6.83V
- Vrtd = 76mV +- 1mV
- Vload = 50mA
Vout | 4.28 | 4.3V
Vrtd | 0.0763
Vtemp | 1.407 | 0.0763*(-8.14228)+2.0523=1.43, low but OK
Vref | 2.471 | Low but OK

### -60C Voltage Regulation Check

### -60C MPPT Check

- -60C Panel Simulator setting
- VOC = 6.83V
- Vrtd = 76mV +- 1mV
- Vout Supercapacitor = 3.3V
Vpanel | 5.75 | 5.8V
Iin | 0.44 | 440mA
Vtemp | 1.402
Some sagging of Vtemp when in MPPT

PASS

- +60C Panel Simulator setting
- VOC = 5.27V
- Vrtd = 124mV
- Vload = 50mA
Vout | 4.28 | 4.3V
Vrtd | 0.1234
Vtemp | 1.028 | 0.1234*(-8.14228)+2.0523=1.047 Low but seems OK
Vref | 2.471 | Low but OK

### +60C Voltage Regulation Check

### +60C MPPT Check

- +60C Panel Simulator setting
- VOC = 5.27V
- Vrtd = 124mV
- Vout Supercapacitor = 3.5V
Vpanel | 4.21 | 4.3… Hmm low
Iin | ~0.440 | 440mA

PASS

### MISC Checks

VREF
MPPT ISOLATION
TL1451Fsw 60C | 471.1 KHz | Quickprint8
Scope Capture -60C | Oscillator MPPT | Quickprint8
Scope Capture +60C | SWNode MPPT | Quickprint 9

## -Z MPPT

- -60C Panel Simulator setting
- VOC = 6.83V
- Vrtd = 76mV +- 1mV
- Vload = 50mA
Vout | 4.29 | 4.3V
Vrtd | .076
Vtemp | 1.416 | 0.076*(-8.14228)+2.0523=1.43, low but OK
Vref | 2.474 | Low but OK

### -60C Voltage Regulation Check

### -60C MPPT Check

- -60C Panel Simulator setting
- VOC = 6.83V
- Vrtd = 76mV +- 1mV
- Vout Supercapacitor = 3.3V
Vpanel | 5.81 | 5.8V
Iin | ~0.44 | 440mA
Vtemp | 1.419
Some sagging of Vtemp when in MPPT

PASS

- +60C Panel Simulator setting
- VOC = 5.27V
- Vrtd = 124mV
- Vload = 50mA
Vout | 4.29 | 4.3V
Vrtd | .1245
Vtemp | 1.025 | 0.1245*(-8.14228)+2.0523=1.03859 Low but seems OK
Vref | 2.474 | Low but OK

### +60C Voltage Regulation Check

### +60C MPPT Check

- +60C Panel Simulator setting
- VOC = 5.27V
- Vrtd = 124mV
- Vout Supercapacitor = 3.3V
Vpanel | 4.21 | 4.3… Hmm pretty low
Iin | ~0.44 | 440mA

PASS

VREF
MPPT ISOLATION
TL1251 Fsw -60C | 475.4KHz
Scope Capture -60C | Oscillator MPPT | Quickprint13
Scope Capture -60C | SW Node MPPT | Quickprint14
Scope Capture +60C | SWNode MPPT | Quickprint 15

### MISC Checks

## +Z MPPT

- -60C Panel Simulator setting
- VOC = 6.83V
- Vrtd = 76mV +- 1mV
- Vload = 50mA
Vout | 4.28 | 4.3V
Vrtd | .077
Vtemp | 1.400 | 0.077*(-8.14228)+2.0523=1.425, low but OK
Vref | 2.47 | Low but OK

### -60C Voltage Regulation Check

### -60C MPPT Check

- -60C Panel Simulator setting
- VOC = 6.83V
- Vrtd = 76mV +- 1mV
- Vout Supercapacitor = 3.3V
Vpanel | 5.74 | 5.8V
Iin | ~0.44 | 440mA
Vtemp | 1.400

PASS

### +60C Voltage Regulation Check

- +60C Panel Simulator setting
- VOC = 5.27V
- Vrtd = 124mV
- Vload = 50mA
Vout | 4.28 | 4.3V
Vrtd | 0.124
Vtemp | 1.020 | 0.124*(-8.14228)+2.0523=1.042 Low but seems OK
Vref | 2.47 | Low but OK

### +60C MPPT Check

- +60C Panel Simulator setting
- VOC = 5.27V
- Vrtd = 124mV
- Vout Supercapacitor = 3.5V
Vpanel | 4.19 | 4.3… Hmm pretty low
Iin | ~0.44 | 440mA

PASS

VREF
MPPT ISOLATION
TL1251 Fsw 60C | 475.8KHz
Scope Capture 60C | Oscillator MPPT | Quickprint18
Scope Capture 60C | SW Node MPPT | Quickprint17
Scope Capture +60C | SWNode MPPT | Quickprint16
Scope Capture -60C | Oscillator MPPT | Quickprint19
Scope Capture -60C | SWNode MPPT | Quickprint20

### MISC Checks

## MPPT Functional Tests

Solar Safe Z+
SolarSafe Z-
SolarSafe X+
SolarSafe X-
SolarSafe Y+
SolarSafe Y-
Connectivity BUS48 -> +Y Deploy Sensor | Only top bus connector
Connectivity BUS50 -> +Y Deploy | Only top bus connector

Connectivity BUS44 -> -Y Deploy Sensor | Only top bus connector
Connectivity BUS46 -> -Y Deploy | Only top bus connector
Current Sense Voltage 0.392A | 0.953V 0.392*0.025*100=0.98 My Imeas inaccurate
U7 Pin 5 Current Sense Voltage
Current Sense Resistor Vdrop @0.392A | 10mV 0.01/0.392=0.0255 Ohms
MPPT +X Cout Noise | Quickprint22,Quickprint24
Vbatt | Quickprint25,Quickprint26

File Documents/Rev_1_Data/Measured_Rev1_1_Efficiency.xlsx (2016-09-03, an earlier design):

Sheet: Summary
25°C Measurements
Component | Median Resistance
MOSFET | 0.029Ω
Inductor | 0.072Ω
LTC4411 | 0.233Ω
Current Sense | 0.026Ω
PI filter | 0.040Ω
Trace | 0.005Ω
Total | 0.404Ω
25°C Theoretical Operation
Parameter | Value
25°C Power | 2.086W | Notes
25°C I_Panel | 0.440A | These measurements were not super accurate, constant current roughly at indicated values
25°C Max I_out | 0.497A
25°C Theoretical Efficiency
Parameter | Value
25°C Resistive Power Loss | 0.098W
25°C Quiescient Power Loss | 0.099W
25°C Efficiency | 90.55%

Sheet: Quiescent
25°C Quiescent Power
VOC | IQ | PQ
4.9 | 0.01516 | 0.074W
5.1 | 0.01573 | 0.080W
5.3 | 0.01628 | 0.086W
5.5 | 0.01669 | 0.092W
5.7 | 0.01738 | 0.099W
5.9 | 0.01775 | 0.105W
6.1 | 0.01852 | 0.113W
6.3 | 0.01882 | 0.119W
6.5 | 0.01943 | 0.126W
Median |  | 0.099W

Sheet: MOSFET
25°C Resistance Measurement
Current | Voltage | Power | Resistance
0.05 | 0.0014 | 7e-05W | 0.028Ω
0.1 | 0.0029 | 0.00029W | 0.029Ω
0.15 | 0.0043 | 0.001W | 0.029Ω
0.2 | 0.0056 | 0.001W | 0.028Ω
0.25 | 0.0072 | 0.002W | 0.029Ω
0.3 | 0.0085 | 0.003W | 0.028Ω
0.35 | 0.01 | 0.003W | 0.029Ω
Median |  |  | 0.029Ω

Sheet: Inductor
Current | Voltage | Power | Resistance
0.05 | 0.0037 | 0.000185W | 0.074Ω
0.1 | 0.0074 | 0.001W | 0.074Ω
0.15 | 0.0107 | 0.002W | 0.071Ω
0.2 | 0.0142 | 0.003W | 0.071Ω
0.25 | 0.0181 | 0.005W | 0.072Ω
0.3 | 0.0212 | 0.006W | 0.071Ω
0.35 | 0.0255 | 0.009W | 0.073Ω
Median |  |  | 0.072Ω

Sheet: LTC4411
Current | Voltage | Power | Resistance
0.05 | 0.0497 | 0.002W | 0.994Ω
0.1 | 0.0608 | 0.006W | 0.608Ω
0.15 | 0.0661 | 0.010W | 0.441Ω
0.2 | 0.0711 | 0.014W | 0.355Ω
0.25 | 0.0755 | 0.019W | 0.302Ω
0.3 | 0.08 | 0.024W | 0.267Ω
0.35 | 0.0848 | 0.030W | 0.242Ω
0.4 | 0.0894 | 0.036W | 0.223Ω
0.45 | 0.0941 | 0.042W | 0.209Ω
0.5 | 0.0987 | 0.049W | 0.197Ω
0.55 | 0.1043 | 0.057W | 0.190Ω
0.6 | 0.1098 | 0.066W | 0.183Ω
0.65 | 0.1149 | 0.075W | 0.177Ω
0.7 | 0.1202 | 0.084W | 0.172Ω
Median |  |  | 0.233Ω

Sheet: ISense
Current | Voltage | Power | Resistance
0.05 | 0.0012 | 6e-05W | 0.024Ω
0.1 | 0.0027 | 0.00027W | 0.027Ω
0.15 | 0.0038 | 0.001W | 0.025Ω
0.2 | 0.0053 | 0.001W | 0.026Ω
0.25 | 0.0063 | 0.002W | 0.025Ω
0.3 | 0.0077 | 0.002W | 0.026Ω
0.35 | 0.009 | 0.003W | 0.026Ω
0.4 | 0.0102 | 0.004W | 0.026Ω
0.45 | 0.0116 | 0.005W | 0.026Ω
0.5 | 0.0129 | 0.006W | 0.026Ω
0.55 | 0.0141 | 0.008W | 0.026Ω
0.6 | 0.0153 | 0.009W | 0.025Ω
0.65 | 0.0166 | 0.011W | 0.026Ω
0.7 | 0.0178 | 0.012W | 0.025Ω
Median |  |  | 0.026Ω

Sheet: PI Inductor
Current | Voltage | Power | Resistance
0.05 | 0.002 | 0.0001W | 0.040Ω
0.1 | 0.004 | 0.0004W | 0.040Ω
0.15 | 0.006 | 0.001W | 0.040Ω
0.2 | 0.008 | 0.002W | 0.040Ω
0.25 | 0.01 | 0.003W | 0.040Ω
0.3 | 0.0123 | 0.004W | 0.041Ω
0.35 | 0.014 | 0.005W | 0.040Ω
0.4 | 0.0163 | 0.007W | 0.041Ω
0.45 | 0.018 | 0.008W | 0.040Ω
0.5 | 0.0203 | 0.010W | 0.041Ω
0.55 | 0.022 | 0.012W | 0.040Ω
0.6 | 0.0245 | 0.015W | 0.041Ω
0.65 | 0.026 | 0.017W | 0.040Ω
0.7 | 0.028 | 0.020W | 0.040Ω
Median |  |  | 0.040Ω

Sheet: MPPT->QSH
Current | Voltage | Power | Resistance
0.05 | 0.0035 | 0.000175W | 0.070Ω
0.1 | 0.0068 | 0.001W | 0.068Ω
0.15 | 0.0107 | 0.002W | 0.071Ω
0.2 | 0.0141 | 0.003W | 0.070Ω
0.25 | 0.0176 | 0.004W | 0.070Ω
0.3 | 0.0213 | 0.006W | 0.071Ω
0.35 | 0.0243 | 0.009W | 0.069Ω
0.4 | 0.0282 | 0.011W | 0.070Ω
0.45 | 0.0315 | 0.014W | 0.070Ω
0.5 | 0.0355 | 0.018W | 0.071Ω
0.55 | 0.0381 | 0.021W | 0.069Ω
0.6 | 0.0423 | 0.025W | 0.070Ω
0.65 | 0.0452 | 0.029W | 0.070Ω
0.7 | 0.0488 | 0.034W | 0.070Ω
Median |  |  | 0.070Ω

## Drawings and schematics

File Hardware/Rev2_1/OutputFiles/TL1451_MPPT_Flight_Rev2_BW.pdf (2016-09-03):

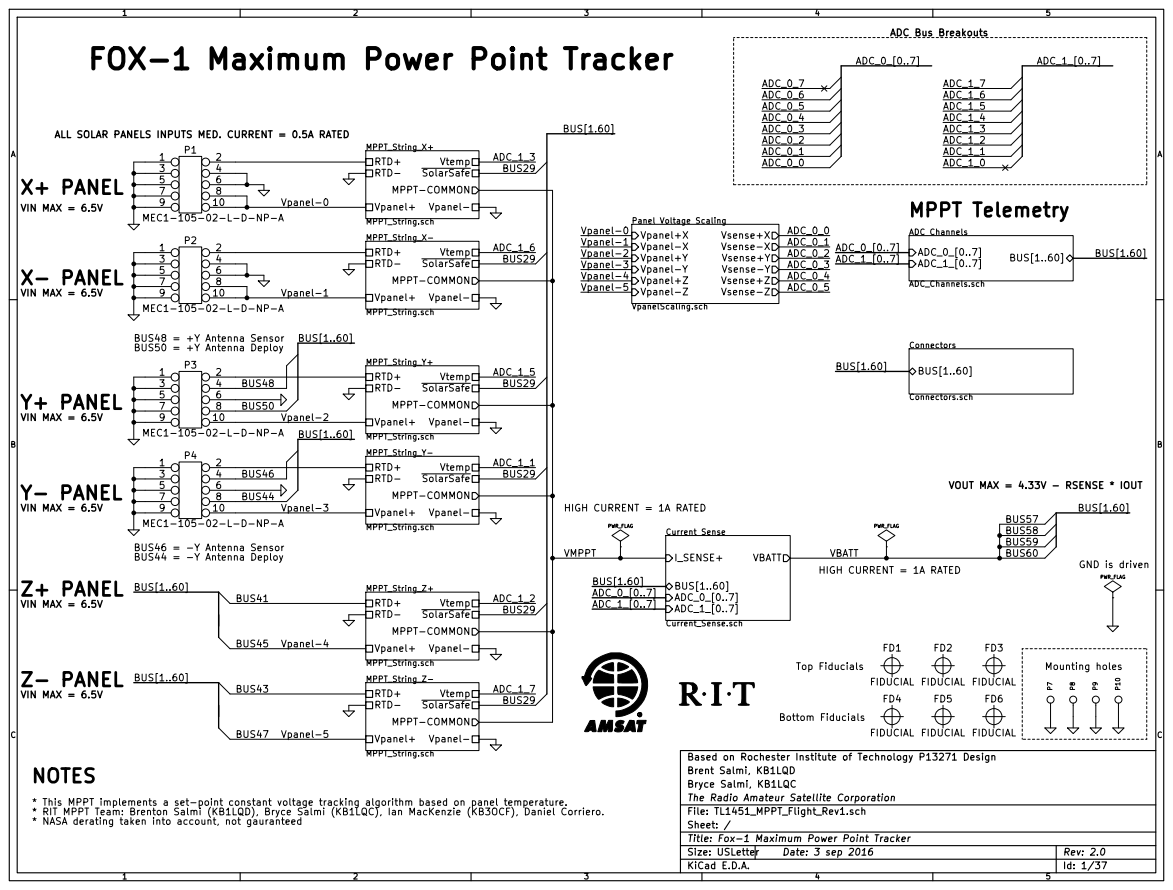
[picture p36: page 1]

ADC Bus Breakouts
MPPT Telemetry
Connectors Connectors.sch BUS[1..60] ADC Channels ADC_Channels.sch ADC_0_[0..7]

FOX-1 Maximum Power Point Tracker

ALL SOLAR PANELS INPUTS MED. CURRENT = 0.5A RATED

VOUT MAX = 4.33V - RSENSE * IOUT VIN MAX = 6.5V

Top Fiducials Bottom Fiducials

Based on Rochester Institute of Technology P13271 Design
Brent Salmi, KB1LQD
Bryce Salmi, KB1LQC
The Radio Amateur Satellite Corporation
Id: 1/37 Title: Fox-1 Maximum Power Point Tracker File: TL1451_MPPT_Flight_Rev1.sch
Sheet: /

* This MPPT implements a set-point constant voltage tracking algorithm based on panel temperature.
* RIT MPPT Team: Brenton Salmi (KB1LQD), Bryce Salmi (KB1LQC), Ian MacKenzie (KB3OCF), Daniel Corriero.
* NASA derating taken into account, not gauranteed

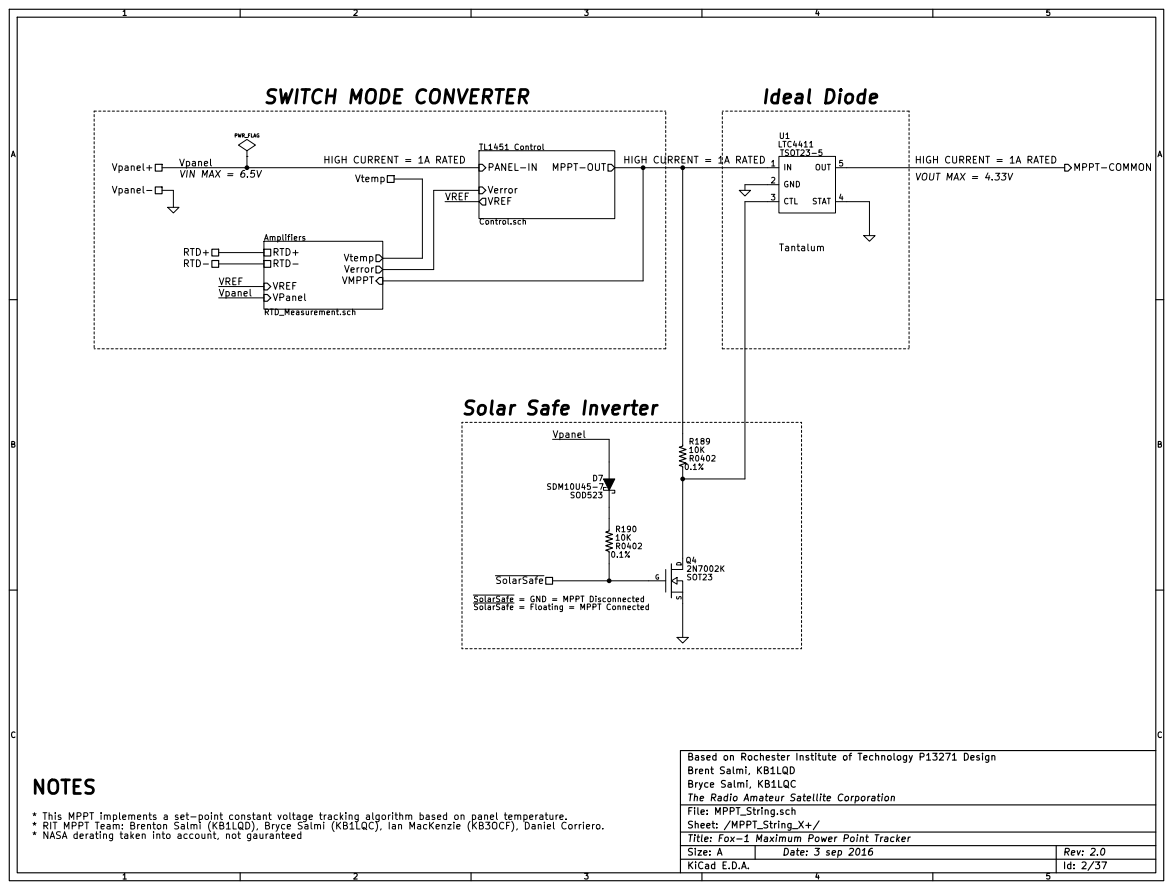
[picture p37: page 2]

Based on Rochester Institute of Technology P13271 Design
Brent Salmi, KB1LQD
Bryce Salmi, KB1LQC
The Radio Amateur Satellite Corporation
Id: 2/37 Title: Fox-1 Maximum Power Point Tracker File: MPPT_String.sch
Sheet: /MPPT_String_X+/

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

DTC GND = 100% capable PWM1 Vpanel

PMOS_PWM

Vpanel

TL1451A reference is very loose Use external reference on next revision.

PWM2 shares oscillator with PWM1 Unusable due to fault propagation
TL1451 failure 1/6th power loss instead of 1/3rd

Based on Rochester Institute of Technology P13271 Design
Brent Salmi, KB1LQD
Bryce Salmi, KB1LQC
The Radio Amateur Satellite Corporation
Id: 3/37 Title: Fox-1 Maximum Power Point Tracker File: Control.sch
Sheet: /MPPT_String_X+/TL1451 Control/

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

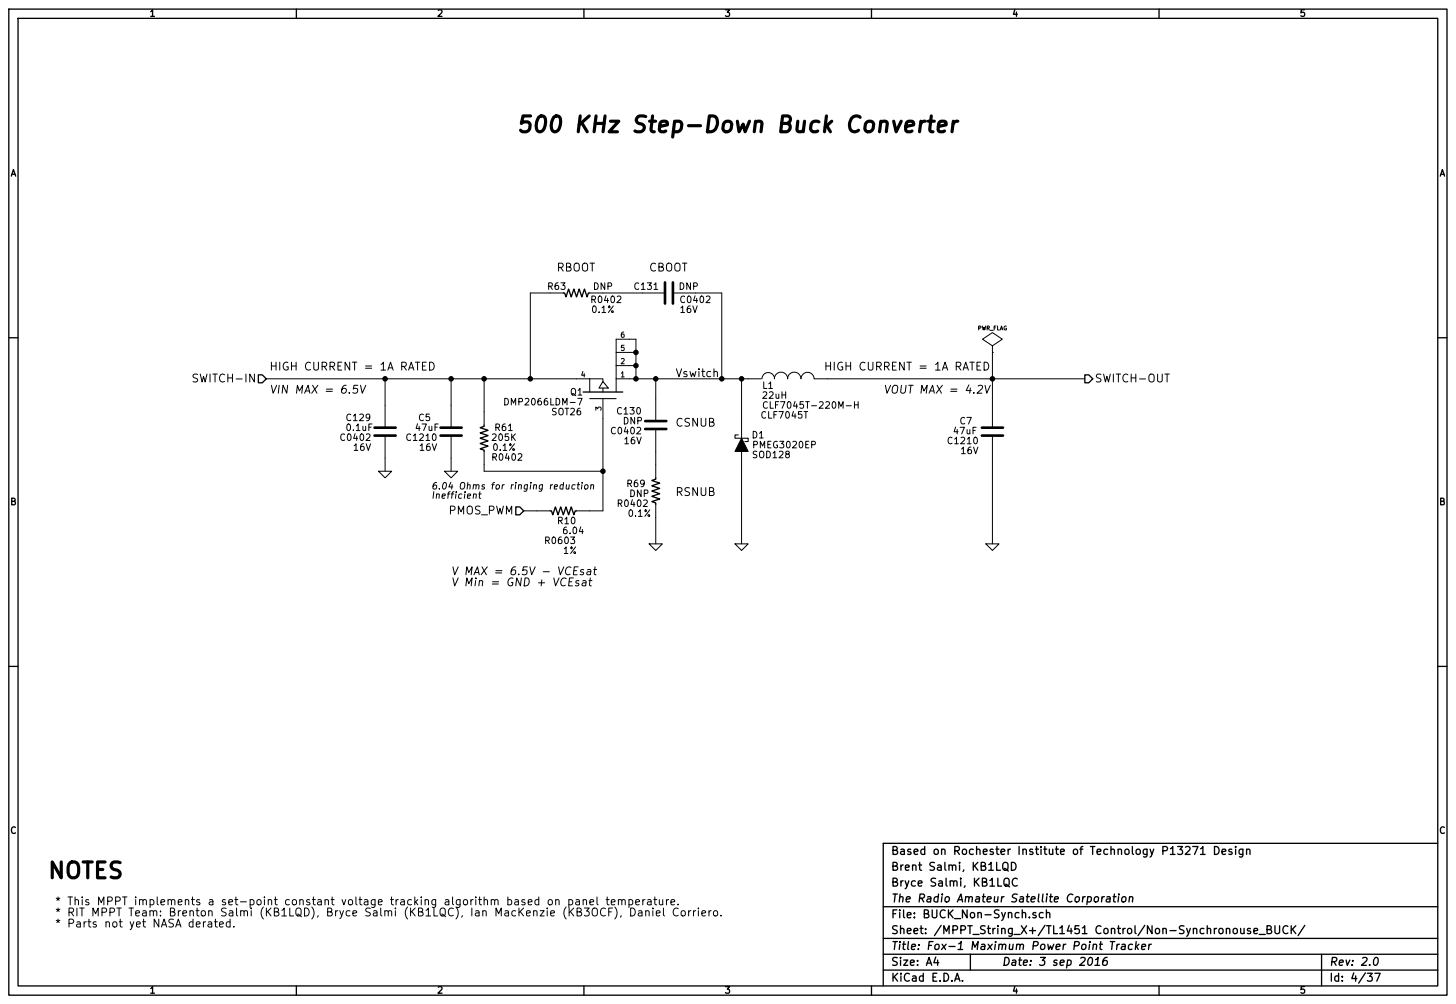
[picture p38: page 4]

16V 500 KHz Step-Down Buck Converter

6.04 Ohms for ringing reduction

Based on Rochester Institute of Technology P13271 Design
Brent Salmi, KB1LQD
Bryce Salmi, KB1LQC
The Radio Amateur Satellite Corporation
Id: 4/37 Title: Fox-1 Maximum Power Point Tracker File: BUCK_Non-Synch.sch
Sheet: /MPPT_String_X+/TL1451 Control/Non-Synchronouse_BUCK/

* This MPPT implements a set-point constant voltage tracking algorithm based on panel temperature.
* RIT MPPT Team: Brenton Salmi (KB1LQD), Bryce Salmi (KB1LQC), Ian MacKenzie (KB3OCF), Daniel Corriero.
* Parts not yet NASA derated.

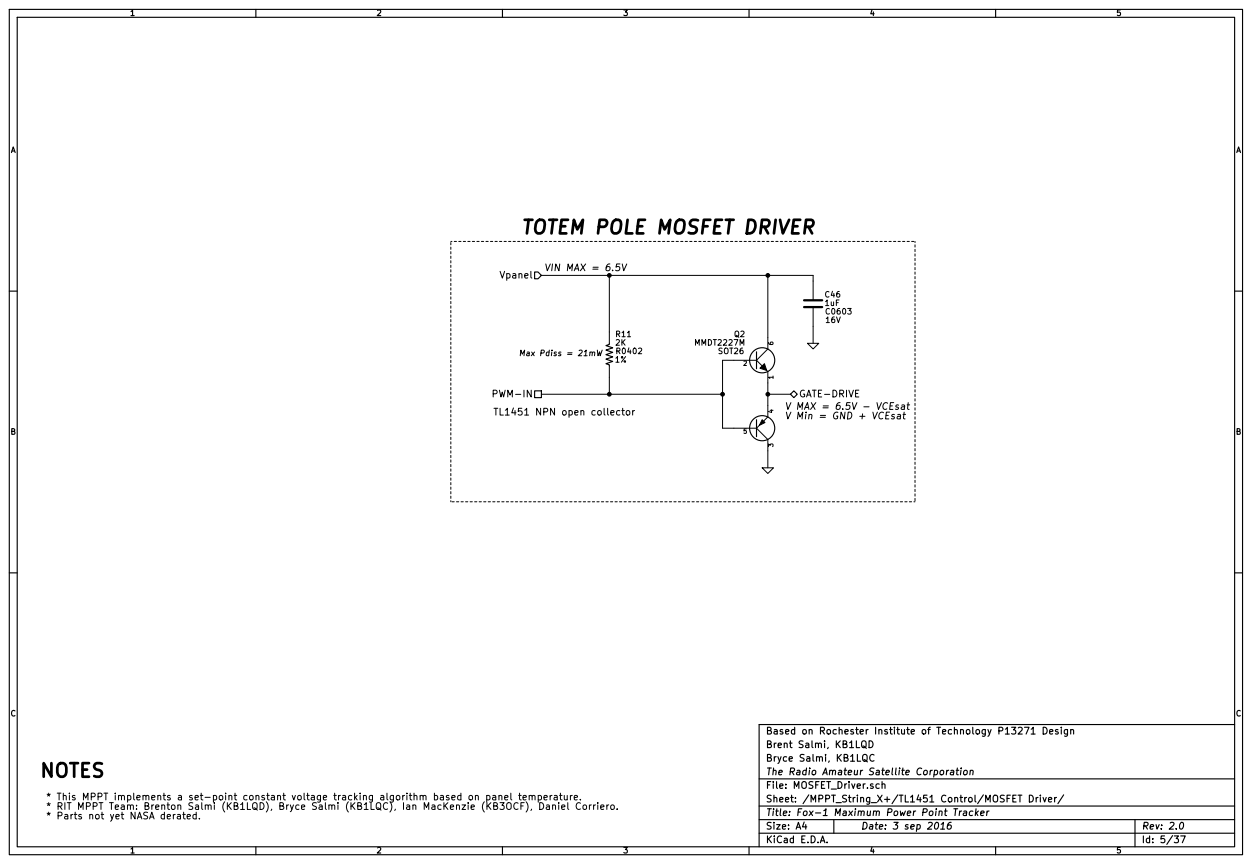
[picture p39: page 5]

TOTEM POLE MOSFET DRIVER

Brent Salmi, KB1LQD
Bryce Salmi, KB1LQC
The Radio Amateur Satellite Corporation
Id: 5/37 Title: Fox-1 Maximum Power Point Tracker File: MOSFET_Driver.sch
Sheet: /MPPT_String_X+/TL1451 Control/MOSFET Driver/

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

TL1451 Voltage Reference = 4% tolerance
This drives error in MPPT regulation

Highest Voltage Wins = Lowest Duty Cycle Wins MPPT = Vout 3.3V to 4.33V

VregError -> Increasing Duty Cycle = Decrease voltage
Regulation = Vout 4.33V, Vpanel increasing

TL1451 Error Amp + PMOS:
Verror Pos = -Duty Cycle

1% Maximum Power Point Tracking Error Amplifier

Based on Rochester Institute of Technology P13271 Design
Brent Salmi, KB1LQD
Bryce Salmi, KB1LQC
The Radio Amateur Satellite Corporation
Id: 6/37 Title: Fox-1 Maximum Power Point Tracker File: RTD_Measurement.sch
Sheet: /MPPT_String_X+/Amplifiers/

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

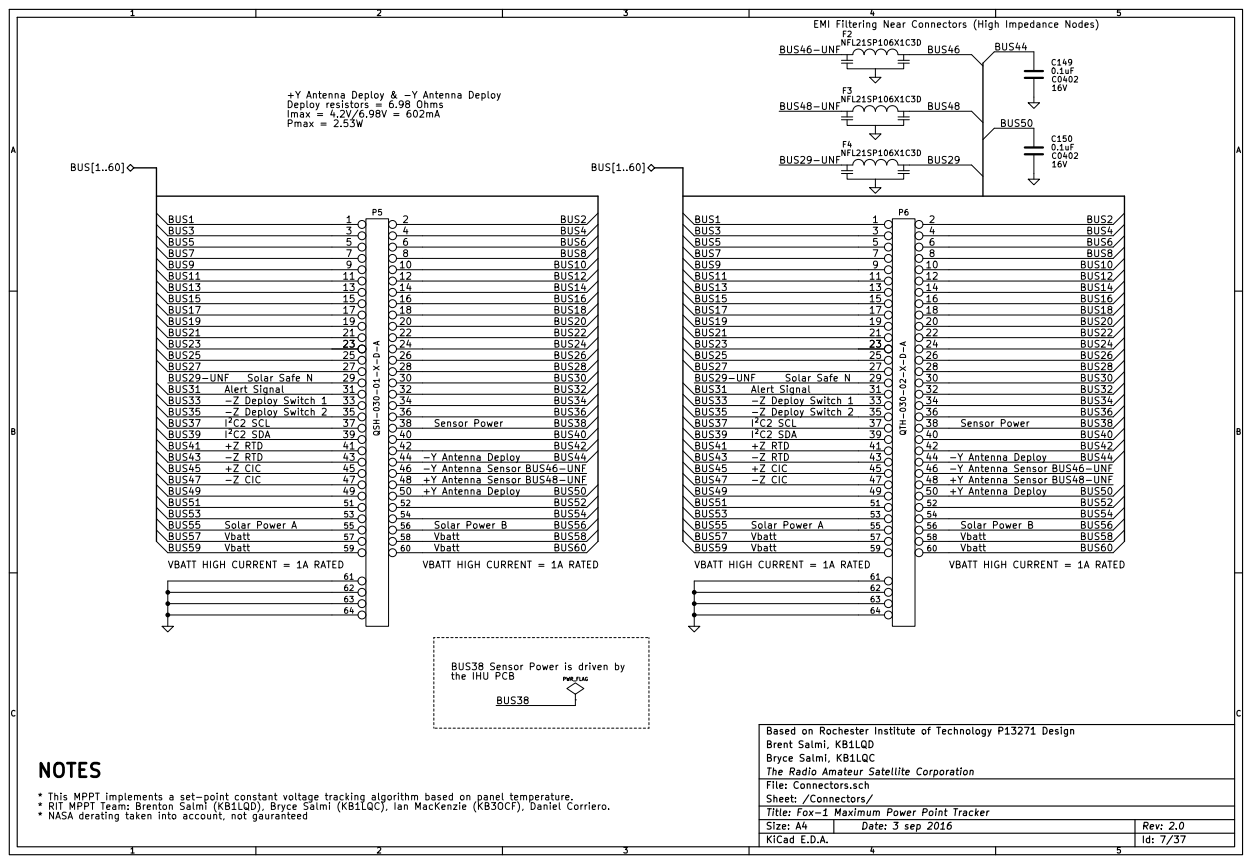
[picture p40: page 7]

+Y Antenna Deploy & -Y Antenna Deploy
Deploy resistors = 6.98 Ohms
Imax = 4.2V/6.98V = 602mA
Pmax = 2.53W

BUS38 Sensor Power is driven by
the IHU PCB

Based on Rochester Institute of Technology P13271 Design
Brent Salmi, KB1LQD
Bryce Salmi, KB1LQC
The Radio Amateur Satellite Corporation
Id: 7/37 Title: Fox-1 Maximum Power Point Tracker File: Connectors.sch
Sheet: /Connectors/
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

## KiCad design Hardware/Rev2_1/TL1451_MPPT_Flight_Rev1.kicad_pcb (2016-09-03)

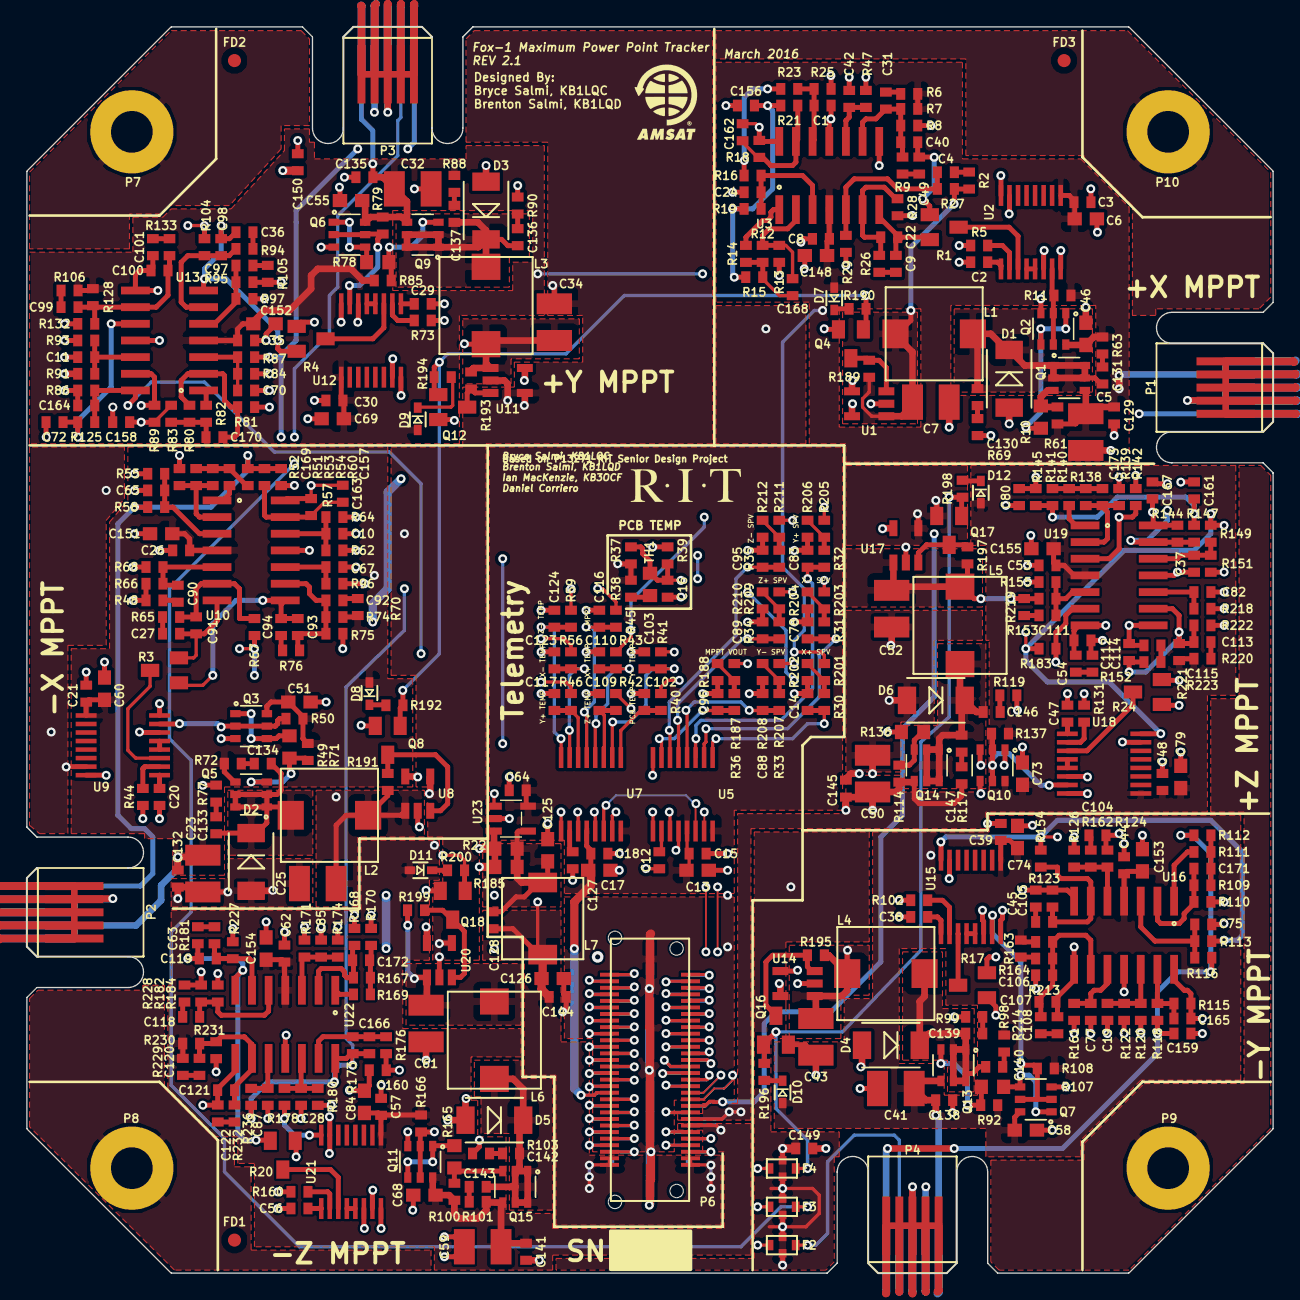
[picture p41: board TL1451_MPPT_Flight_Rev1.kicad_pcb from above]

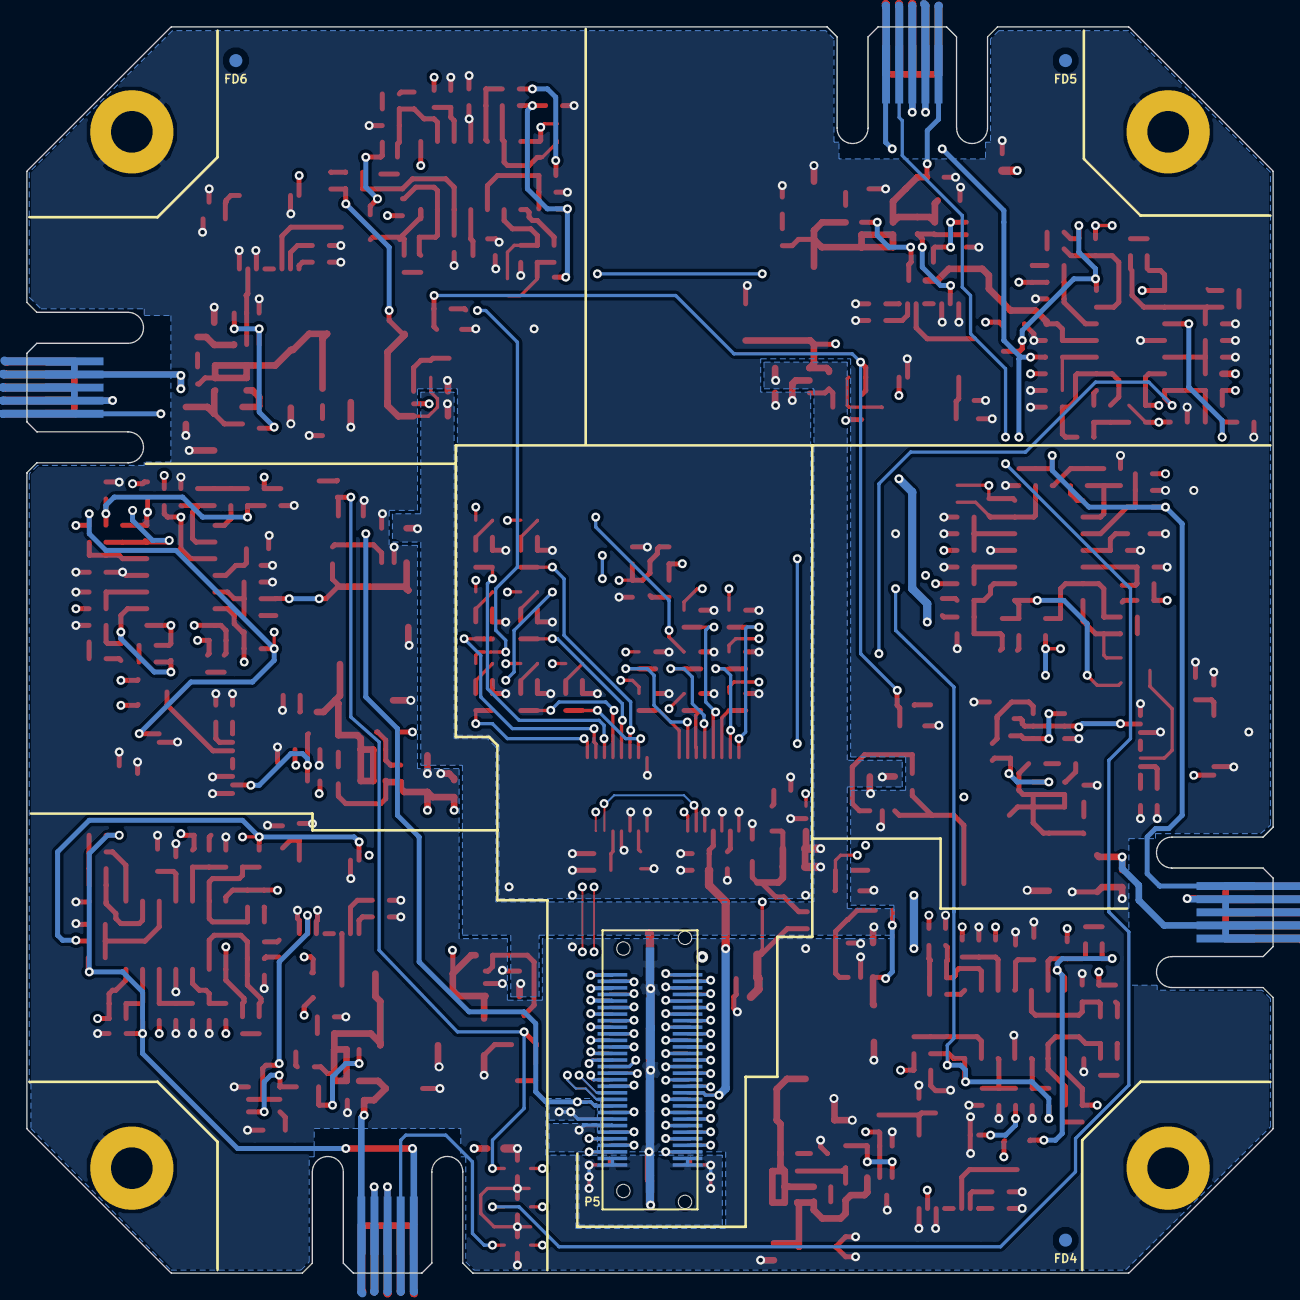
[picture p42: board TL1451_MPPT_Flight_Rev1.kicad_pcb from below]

Board: 4 copper layers, 95.0 x 95.0 mm, 455 parts (4 on the bottom side), 284 nets.

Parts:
C1, C3, C8, C10, C11, C15, C16, C18, C19, C21, C24, C26, C28, C30, C35, C37, C39, C44, C48, C53, C57, C62, C64, C65, C70, C75, C80, C85, C129, C132, C135, C138, C141, C144, C145, C149, C150, C156, C157, C158, C159, C160, C161, C162, C163, C164, C165, C166, C167, C168, C169, C170, C171, C172, C173: 0.1uF; C0402
C2, C20, C29, C38, C47, C56: 220pF; C0402
C4, C31, C90, C92, C97, C99, C104, C106, C111, C113, C118, C120: 0.012uF; C0402
C5, C7, C23, C25, C32, C34, C41, C43, C50, C52, C59, C61: 47uF; C1210
C6, C13, C17, C46, C51, C55, C58, C60, C68, C69, C73, C74, C79, C84, C148, C151, C152, C153, C154, C155: 1uF; C0603
C9, C27, C36, C45, C49, C54, C63, C94, C101, C108, C115, C122: 0.015uF; C0402
C12, C14, C42, C67, C72, C77, C78, C82, C83, C87, C88, C89, C95, C96, C102, C103, C109, C110, C116, C117, C123, C124, C127: 1uF; C0402
C22, C40, C91, C93, C98, C100, C105, C107, C112, C114, C119, C121: 820pF; C0402
C125, C126: 0.39uF; C0603
C128: 0.01uF; C0402
C130, C131, C133, C134, C136, C137, C139, C140, C142, C143, C146, C147: DNP; C0402
D1, D2, D3, D4, D5, D6: PMEG3020EP; SOD128
D7, D8, D9, D10, D11, D12: SDM10U45-7; SOD523
F2, F3, F4: NFL21SP106X1C3D; NFL21SP
FD1, FD2, FD3, FD4, FD5, FD6: FIDUCIAL; FD1
G1: AMSAT_LOGO_SMALL; AMSAT_Logo_Small
G2: RIT_LOGO_SMALL; RIT_Logo_Small
L1, L2, L3, L4, L5, L6: 22uH; CLF7045T
L7: 10uH; SLF6045
P1, P2, P3, P4: CONN_5X2; MEC1-105-02-L-D-NP-A
P5: QSH-030-01-X-D-A; QSH-030-01-L-D-A
P6: QTH-030-02-X-D-A; QTH-030-02-L-D-A
P7, P8, P9, P10: CONN_1; FOX_Mounting_Hole
Q1, Q5, Q9, Q13, Q14, Q15: DMP2066LDM-7; SOT26
Q2, Q3, Q6, Q7, Q10, Q11: MMDT2227M; SOT26
Q4, Q8, Q12, Q16, Q17, Q18: 2N7002K; SOT23
R1, R3, R4, R17, R20, R24: MPMT4001AT1; SOT23
R2, R6, R48, R70, R105, R106, R162, R163, R219, R220, R228, R229: 261; R0402
R5, R44, R73, R102, R131, R160: 4.99K; R0402
R7, R27, R66, R74, R95, R124, R128, R153, R164, R182, R221, R230: 4.75K; R0402
R8, R75, R132, R213, R222, R231: 1.54K; R0402
R9, R21, R26, R60, R65, R76, R89, R94, R118, R123, R133, R147, R152, R176, R181, R214, R223, R232: 3.32K; R0402
R10, R49, R78, R107, R136, R165: 6.04; R0603
R11, R50, R79, R108, R137, R166: 2K; R0402
R12, R13, R16, R19, R51, R52, R55, R58, R80, R81, R84, R87, R109, R110, R113, R116, R138, R139, R142, R145, R167, R168, R171, R174: 249K; R0402
R14, R53, R82, R111, R140, R169: 100; R0402
R15, R54, R83, R112, R141, R170: 2.49K; R0402
R18, R57, R86, R115, R144, R173: 27K; R0402
R22, R185: 0.051; R0603
R23, R62, R91, R120, R149, R178: 24.3K; R0402
R25, R64, R93, R122, R151, R180: 2.4K; R0402
R28, R30, R31, R32, R33, R34, R35, R36, R40, R41, R42, R43, R45, R46, R56, R59, R67, R104, R154, R183, R189, R190, R191, R192, R193, R194, R195, R196, R197, R198, R199, R200, R227: 10K; R0402
R29, R68, R97, R126, R155, R184: 6.49K; R0402
R37: 71.5K; R0402
R38: 330; R0402
R39: 9.09K; R0402
R47, R96, R125, R161, R218, R236: 47K; R0402
R61, R71, R85, R92, R100, R114: 205K; R0402
R63, R69, R72, R77, R88, R90, R98, R99, R101, R103, R117, R119: DNP; R0402
R187, R202, R204, R206, R208, R210, R212: 30.1K; R0402
R188: 40.2K; R0402
R201, R203, R205, R207, R209, R211: 51.1K; R0402
TH1: NTCS0603E3103FMT; R0603
U1, U8, U11, U14, U17, U20: LTC4411; TSOT23-5
U2, U9, U12, U15, U18, U21: TL1451A; PW16
U3, U10, U13, U16, U19, U22: LM6144A; SO14
U5, U7: ADS7828; PW16
U23: INA195; SOT23-5

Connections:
/ADC Channels/Temperature & Current ADC/I2C_SCL: P5.37, P6.37, U5.14, U7.14
/ADC Channels/Temperature & Current ADC/I2C_SDA: P5.39, P6.39, U5.15, U7.15
/ADC Channels/Temperature & Current ADC/MPPT-OUTPUT-CURRENT: R45.1, U23.1
/ADC Channels/Temperature & Current ADC/SENSOR_POWER: C13.1, C15.1, C17.1, C18.1, C64.1, P5.38, P6.38, R37.1, R38.1, U5.13, U5.16, U7.12, U7.16, U23.5
/ADC Channels/Voltage Sense ADC/VMPPT: R36.1, R187.2, R188.1
/BUS44: C149.1, P4.8, P5.44, P6.44
/BUS46: F2.3, P4.4
/BUS48: F3.3, P3.4
/BUS50: C150.1, P3.8, P5.50, P6.50
/Connectors/BUS1: P5.1, P6.1
/Connectors/BUS2: P5.2, P6.2
/Connectors/BUS3: P5.3, P6.3
/Connectors/BUS4: P5.4, P6.4
/Connectors/BUS5: P5.5, P6.5
/Connectors/BUS6: P5.6, P6.6
/Connectors/BUS7: P5.7, P6.7
/Connectors/BUS8: P5.8, P6.8
/Connectors/BUS9: P5.9, P6.9
/Connectors/BUS10: P5.10, P6.10
/Connectors/BUS11: P5.11, P6.11
/Connectors/BUS12: P5.12, P6.12
/Connectors/BUS13: P5.13, P6.13
/Connectors/BUS14: P5.14, P6.14
/Connectors/BUS15: P5.15, P6.15
/Connectors/BUS16: P5.16, P6.16
/Connectors/BUS17: P5.17, P6.17
/Connectors/BUS18: P5.18, P6.18
/Connectors/BUS19: P5.19, P6.19
/Connectors/BUS20: P5.20, P6.20
/Connectors/BUS21: P5.21, P6.21
/Connectors/BUS22: P5.22, P6.22
/Connectors/BUS23: P5.23, P6.23
/Connectors/BUS24: P5.24, P6.24
/Connectors/BUS25: P5.25, P6.25
/Connectors/BUS26: P5.26, P6.26
/Connectors/BUS27: P5.27, P6.27
/Connectors/BUS28: P5.28, P6.28
/Connectors/BUS29-UNF: F4.1, P5.29, P6.29
/Connectors/BUS30: P5.30, P6.30
/Connectors/BUS31: P5.31, P6.31
/Connectors/BUS32: P5.32, P6.32
/Connectors/BUS33: P5.33, P6.33
/Connectors/BUS34: P5.34, P6.34
/Connectors/BUS35: P5.35, P6.35
/Connectors/BUS36: P5.36, P6.36
/Connectors/BUS40: P5.40, P6.40
/Connectors/BUS42: P5.42, P6.42
/Connectors/BUS46-UNF: F2.1, P5.46, P6.46
/Connectors/BUS48-UNF: F3.1, P5.48, P6.48
/Connectors/BUS49: P5.49, P6.49
/Connectors/BUS51: P5.51, P6.51
/Connectors/BUS52: P5.52, P6.52
/Connectors/BUS53: P5.53, P6.53
/Connectors/BUS54: P5.54, P6.54
/Connectors/BUS55: P5.55, P6.55
/Connectors/BUS56: P5.56, P6.56
/Current Sense/I_SENSE+: R22.1, R185.1, U1.5, U8.5, U11.5, U14.5, U17.5, U20.5, U23.3
/Current Sense/Sense-: C125.1, C128.1, L7.1, R22.2, R185.2, U23.4
/Current Sense/VBATT: C126.1, C128.2, C144.1, L7.2, P5.57, P5.58, P5.59, P5.60, P6.57, P6.58, P6.59, P6.60, R187.1
/MPPT_String_X+/Amplifiers/VREF: R16.1, R23.1, R28.1, U2.16
/MPPT_String_X+/Amplifiers/Verror: R1.3, U2.3
/MPPT_String_X+/RTD+: C156.2, P1.2, R15.2, R19.2, R21.1
/MPPT_String_X+/TL1451 Control/MOSFET Driver/GATE-DRIVE: Q2.1, Q2.4, R10.1
/MPPT_String_X+/TL1451 Control/MOSFET Driver/PWM-IN: Q2.2, Q2.5, R11.2, U2.7
/MPPT_String_X+/TL1451 Control/MPPT-OUT: C7.1, L1.2, R2.1, R27.1, R189.1, U1.1
/MPPT_String_X+/TL1451 Control/Non-Synchronouse_BUCK/Vswitch: C130.1, C131.2, D1.1, L1.1, Q1.1, Q1.2, Q1.5, Q1.6
/MPPT_String_X+/Vpanel+: C3.1, C5.1, C6.1, C8.1, C46.1, C129.1, C148.1, D7.2, P1.8, P1.10, Q1.4, Q2.6, R6.1, R7.1, R11.1, R61.1, R63.1, R201.1, U2.9, U3.4
/MPPT_String_X+/Vtemp: C162.1, R18.2, R43.1, R47.1, U3.14
/MPPT_String_X+/~SolarSafe~: F4.3, Q4.1, Q8.1, Q12.1, Q16.1, Q17.1, Q18.1, R190.2, R192.2, R194.2, R196.2, R198.2, R200.2
/MPPT_String_X-/Amplifiers/VREF: R55.1, R62.1, R67.1, U9.16
/MPPT_String_X-/Amplifiers/Verror: R3.3, U9.3
/MPPT_String_X-/RTD+: C157.2, P2.2, R54.2, R58.2, R60.1
/MPPT_String_X-/TL1451 Control/MOSFET Driver/GATE-DRIVE: Q3.1, Q3.4, R49.1
/MPPT_String_X-/TL1451 Control/MOSFET Driver/PWM-IN: Q3.2, Q3.5, R50.2, U9.7
/MPPT_String_X-/TL1451 Control/MPPT-OUT: C25.1, L2.2, R48.1, R66.1, R191.1, U8.1
/MPPT_String_X-/TL1451 Control/Non-Synchronouse_BUCK/Vswitch: C133.1, C134.2, D2.1, L2.1, Q5.1, Q5.2, Q5.5, Q5.6
/MPPT_String_X-/Vpanel+: C21.1, C23.1, C26.1, C51.1, C60.1, C132.1, C151.1, D8.2, P2.8, P2.10, Q3.6, Q5.4, R50.1, R70.1, R71.1, R72.1, R74.1, R203.1, U9.9, U10.4
/MPPT_String_X-/Vtemp: C163.1, R56.1, R57.2, R96.1, U10.14
/MPPT_String_Y+/Amplifiers/VREF: R84.1, R91.1, R104.1, U12.16
/MPPT_String_Y+/Amplifiers/Verror: R4.3, U12.3
/MPPT_String_Y+/RTD+: C158.2, P3.2, R83.2, R87.2, R89.1
/MPPT_String_Y+/TL1451 Control/MOSFET Driver/GATE-DRIVE: Q6.1, Q6.4, R78.1
/MPPT_String_Y+/TL1451 Control/MOSFET Driver/PWM-IN: Q6.2, Q6.5, R79.2, U12.7
/MPPT_String_Y+/TL1451 Control/MPPT-OUT: C34.1, L3.2, R95.1, R105.1, R193.1, U11.1
/MPPT_String_Y+/TL1451 Control/Non-Synchronouse_BUCK/Vswitch: C136.1, C137.2, D3.1, L3.1, Q9.1, Q9.2, Q9.5, Q9.6
/MPPT_String_Y+/Vpanel+: C30.1, C32.1, C35.1, C55.1, C69.1, C135.1, C152.1, D9.2, P3.10, Q6.6, Q9.4, R79.1, R85.1, R88.1, R106.1, R128.1, R205.1, U12.9, U13.4
/MPPT_String_Y+/Vtemp: C164.1, R46.1, R86.2, R125.1, U13.14
/MPPT_String_Y-/Amplifiers/VREF: R113.1, R120.1, R154.1, U15.16
/MPPT_String_Y-/Amplifiers/Verror: R17.3, U15.3
/MPPT_String_Y-/RTD+: C159.2, P4.2, R112.2, R116.2, R118.1
/MPPT_String_Y-/TL1451 Control/MOSFET Driver/GATE-DRIVE: Q7.1, Q7.4, R107.1
/MPPT_String_Y-/TL1451 Control/MOSFET Driver/PWM-IN: Q7.2, Q7.5, R108.2, U15.7
/MPPT_String_Y-/TL1451 Control/MPPT-OUT: C43.1, L4.2, R124.1, R162.1, R195.1, U14.1
/MPPT_String_Y-/TL1451 Control/Non-Synchronouse_BUCK/Vswitch: C139.1, C140.2, D4.1, L4.1, Q13.1, Q13.2, Q13.5, Q13.6
/MPPT_String_Y-/Vpanel+: C39.1, C41.1, C44.1, C58.1, C74.1, C138.1, C153.1, D10.2, P4.10, Q7.6, Q13.4, R92.1, R98.1, R108.1, R163.1, R164.1, R207.1, U15.9, U16.4
/MPPT_String_Y-/Vtemp: C165.1, R41.1, R115.2, R161.1, U16.14
/MPPT_String_Z+/Amplifiers/VREF: R142.1, R149.1, R183.1, U18.16
/MPPT_String_Z+/Amplifiers/Verror: R24.3, U18.3
/MPPT_String_Z+/RTD+: C161.2, P5.41, P6.41, R141.2, R145.2, R147.1
/MPPT_String_Z+/TL1451 Control/MOSFET Driver/GATE-DRIVE: Q10.1, Q10.4, R136.1
/MPPT_String_Z+/TL1451 Control/MOSFET Driver/PWM-IN: Q10.2, Q10.5, R137.2, U18.7
/MPPT_String_Z+/TL1451 Control/MPPT-OUT: C52.1, L5.2, R153.1, R197.1, R219.1, U17.1
/MPPT_String_Z+/TL1451 Control/Non-Synchronouse_BUCK/Vswitch: C146.1, C147.2, D6.1, L5.1, Q14.1, Q14.2, Q14.5, Q14.6
/MPPT_String_Z+/Vpanel+: C48.1, C50.1, C53.1, C73.1, C79.1, C145.1, C155.1, D12.2, P5.45, P6.45, Q10.6, Q14.4, R114.1, R117.1, R137.1, R209.1, R220.1, R221.1, U18.9, U19.4
/MPPT_String_Z+/Vtemp: C167.1, R42.1, R144.2, R218.1, U19.14
/MPPT_String_Z-/Amplifiers/VREF: R171.1, R178.1, R227.1, U21.16
/MPPT_String_Z-/Amplifiers/Verror: R20.3, U21.3
/MPPT_String_Z-/RTD+: C160.2, P5.43, P6.43, R170.2, R174.2, R176.1
/MPPT_String_Z-/TL1451 Control/MOSFET Driver/GATE-DRIVE: Q11.1, Q11.4, R165.1
/MPPT_String_Z-/TL1451 Control/MOSFET Driver/PWM-IN: Q11.2, Q11.5, R166.2, U21.7
/MPPT_String_Z-/TL1451 Control/MPPT-OUT: C61.1, L6.2, R182.1, R199.1, R228.1, U20.1
/MPPT_String_Z-/TL1451 Control/Non-Synchronouse_BUCK/Vswitch: C142.1, C143.2, D5.1, L6.1, Q15.1, Q15.2, Q15.5, Q15.6
/MPPT_String_Z-/Vpanel+: C57.1, C59.1, C62.1, C68.1, C84.1, C141.1, C154.1, D11.2, P5.47, P6.47, Q11.6, Q15.4, R100.1, R101.1, R166.1, R211.1, R229.1, R230.1, U21.9, U22.4
/MPPT_String_Z-/Vtemp: C166.1, R59.1, R173.2, R236.1, U22.14
/Panel Voltage Scaling/Vsense+X: R30.1, R201.2, R202.1
/Panel Voltage Scaling/Vsense+Y: R32.1, R205.2, R206.1
/Panel Voltage Scaling/Vsense+Z: R34.1, R209.2, R210.1
/Panel Voltage Scaling/Vsense-X: R31.1, R203.2, R204.1
/Panel Voltage Scaling/Vsense-Y: R33.1, R207.2, R208.1
/Panel Voltage Scaling/Vsense-Z: R35.1, R211.2, R212.1
GND: C1.1, C2.2, C3.2, C5.2, C6.2, C7.2, C8.2, C10.1, C11.1, C12.2, C13.2, C14.2, C15.2, C16.2, C17.2, C18.2, C19.1, C20.2, C21.2, C23.2, C24.1, C25.2, C26.2, C28.1, C29.2, C30.2, C32.2, C34.2, C35.2, C37.1, C38.2, C39.2, C41.2, C42.1, C43.2, C44.2, C46.2, C47.2, C48.2, C50.2, C51.2, C52.2, C53.2, C55.2, C56.2, C57.2, C58.2, C59.2, C60.2, C61.2, C62.2, C64.2, C65.1, C67.1, C68.2, C69.2, C70.1, C72.1, C73.2, C74.2, C75.1, C77.1, C78.2, C79.2, C80.1, C82.1, C83.2, C84.2, C85.1, C87.1, C88.2, C89.2, C95.2, C96.2, C102.2, C103.2, C109.2, C110.2, C116.2, C117.2, C123.2, C124.2, C125.2, C126.2, C127.2, C129.2, C132.2, C135.2, C138.2, C141.2, C144.2, C145.2, C148.2, C149.2, C150.2, C151.2, C152.2, C153.2, C154.2, C155.2, C156.1, C157.1, C158.1, C159.1, C160.1, C161.1, D1.2, D2.2, D3.2, D4.2, D5.2, D6.2, F2.2, F3.2, F4.2, P1.1, P1.3, P1.4, P1.5, P1.6, P1.7, P1.9, P2.1, P2.3, P2.4, P2.5, P2.6, P2.7, P2.9, P3.1, P3.3, P3.5, P3.6, P3.7, P3.9, P4.1, P4.3, P4.5, P4.6, P4.7, P4.9, P5.61, P5.62, P5.63, P5.64, P6.61, P6.62, P6.63, P6.64, P7.1, P8.1, P9.1, P10.1, Q2.3, Q3.3, Q4.2, Q6.3, Q7.3, Q8.2, Q10.3, Q11.3, Q12.2, Q16.2, Q17.2, Q18.2, R5.2, R8.2, R13.1, R25.2, R29.2, R39.2, R44.2, R52.1, R64.2, R68.2, R69.2, R73.2, R75.2, R77.2, R81.1, R90.2, R93.2, R97.2, R99.2, R102.2, R103.2, R110.1, R119.2, R122.2, R126.2, R131.2, R132.2, R139.1, R151.2, R155.2, R160.2, R168.1, R180.2, R184.2, R188.2, R202.2, R204.2, R206.2, R208.2, R210.2, R212.2, R213.2, R222.2, R231.2, U1.2, U1.4, U2.6, U2.8, U2.15, U3.11, U5.8, U5.9, U5.11, U5.12, U7.9, U7.11, U7.13, U8.2, U8.4, U9.6, U9.8, U9.15, U10.11, U11.2, U11.4, U12.6, U12.8, U12.15, U13.11, U14.2, U14.4, U15.6, U15.8, U15.15, U16.11, U17.2, U17.4, U18.6, U18.8, U18.15, U19.11, U20.2, U20.4, U21.6, U21.8, U21.15, U22.11, U23.2
unnamed: Q4.3, R189.2, U1.3
unnamed: D7.1, R190.1
unnamed: D8.1, R192.1
unnamed: Q8.3, R191.2, U8.3
unnamed: D9.1, R194.1
unnamed: Q12.3, R193.2, U11.3
unnamed: D10.1, R196.1
unnamed: Q16.3, R195.2, U14.3
unnamed: Q17.3, R197.2, U17.3
unnamed: D12.1, R198.1
unnamed: Q18.3, R199.2, U20.3
unnamed: D11.1, R200.1
unnamed: U2.4, U2.5
unnamed: R5.1, U2.2
unnamed: C2.1, U2.1
unnamed: C1.2, R23.2, R25.1, U3.12
unnamed: C31.2, C40.1, R7.2, R8.1, R9.1, U3.9
unnamed: C168.1, R12.1, R13.2, U3.2
unnamed: C168.2, R12.2, R14.2, R15.1
unnamed: R14.1, U3.1
unnamed: C49.1, R9.2
unnamed: C4.1, R2.2
unnamed: C31.1, R6.2
unnamed: C9.1, R26.2
unnamed: C22.1, R26.1, R28.2, U3.6
unnamed: C4.2, R27.2, R29.1, U3.5
unnamed: C42.2, R47.2, U3.10
unnamed: C40.2, C49.2, R1.1, U3.8
unnamed: C9.2, C22.2, R1.2, U3.7
unnamed: C24.2, R16.2, R19.1, U3.3
unnamed: C162.2, R18.1, R21.2, U3.13
unnamed: C96.1, R36.2, U5.7
unnamed: C12.1, U5.10
unnamed: C95.1, R35.2, U5.6
unnamed: C14.1, R30.2, U5.1
unnamed: C89.1, R34.2, U5.5
unnamed: C88.1, R33.2, U5.4
unnamed: C83.1, R32.2, U5.3
unnamed: C78.1, R31.2, U5.2
unnamed: C116.1, R45.2, U7.5
unnamed: C110.1, R43.2, U7.4
unnamed: C109.1, R42.2, U7.3
unnamed: C103.1, R41.2, U7.2
unnamed: R38.2, TH1.1
unnamed: C124.1, R59.2, U7.8
unnamed: C123.1, R56.2, U7.7
unnamed: C127.1, U7.10
unnamed: C102.1, R40.2, U7.1
unnamed: C117.1, R46.2, U7.6
unnamed: C16.1, R37.2, R39.1, R40.1, TH1.2
unnamed: U9.4, U9.5
unnamed: R44.1, U9.2
unnamed: C20.1, U9.1
unnamed: C67.2, R96.2, U10.10
unnamed: C163.2, R57.1, R60.2, U10.13
unnamed: C27.2, C91.2, R3.2, U10.7
unnamed: C27.1, R65.2
unnamed: C93.2, C94.2, R3.1, U10.8
unnamed: C94.1, R76.2
unnamed: C92.2, C93.1, R74.2, R75.1, R76.1, U10.9
unnamed: C92.1, R70.2
unnamed: C90.2, R66.2, R68.1, U10.5
unnamed: C90.1, R48.2
unnamed: C10.2, R62.2, R64.1, U10.12
unnamed: C91.1, R65.1, R67.2, U10.6
unnamed: C65.2, R55.2, R58.1, U10.3
unnamed: C169.1, R51.1, R52.2, U10.2
unnamed: R53.1, U10.1
unnamed: C169.2, R51.2, R53.2, R54.1
unnamed: C29.1, U12.1
unnamed: R73.1, U12.2
unnamed: U12.4, U12.5
unnamed: C72.2, R125.2, U13.10
unnamed: C99.1, R106.2
unnamed: C97.1, R105.2
unnamed: C97.2, R95.2, R97.1, U13.5
unnamed: C98.1, R94.1, R104.2, U13.6
unnamed: C36.1, R94.2
unnamed: C99.2, C100.1, R128.2, R132.1, R133.1, U13.9
unnamed: C101.1, R133.2
unnamed: C170.2, R80.2, R82.2, R83.1
unnamed: C100.2, C101.2, R4.1, U13.8
unnamed: C70.2, R84.2, R87.1, U13.3
unnamed: C170.1, R80.1, R81.2, U13.2
unnamed: R82.1, U13.1
unnamed: C36.2, C98.2, R4.2, U13.7
unnamed: C164.2, R86.1, R89.2, U13.13
unnamed: C11.2, R91.2, R93.1, U13.12
unnamed: U15.4, U15.5
unnamed: R102.1, U15.2
unnamed: C38.1, U15.1
unnamed: C165.2, R115.1, R118.2, U16.13
unnamed: C45.1, R123.2
unnamed: C108.1, R214.2
unnamed: C105.1, R123.1, R154.2, U16.6
unnamed: C104.1, R162.2
unnamed: R111.1, U16.1
unnamed: C171.2, R109.2, R111.2, R112.1
unnamed: C171.1, R109.1, R110.2, U16.2
unnamed: C75.2, R113.2, R116.1, U16.3
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

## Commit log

2016-09-03 Adding images of Rev 2 MPPT PCBA
2016-09-03 Added initial hardware files and a few directories
    [ADC_Channels.sch, ADC_Temp_Current.sch, ADC_Voltage_Sense.sch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]
2016-09-03 Adding initial MPPT design files and updated documentation. May need some more work to clean up but mostly there.
    [ADC_Channels.sch, ADC_Temp_Current.sch, ADC_Voltage_Sense.sch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]
